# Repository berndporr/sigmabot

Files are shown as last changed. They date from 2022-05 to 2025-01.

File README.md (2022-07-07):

# sigmabot
Robot with linear servos and LIDAR

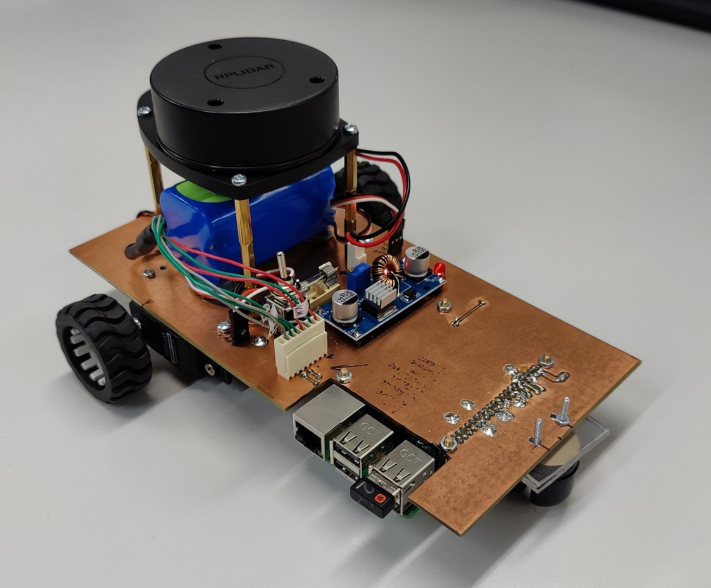
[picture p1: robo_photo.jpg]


## Power supply

TODO. Needs to be fixed.

## LiDAR

RPLIDAR A1M8 is a 360degree omnidirectional laser scanner, based on the
triangulation ranging technique that emits modulated laser signal in
the near-infrared (NIR) light band (typ. 785nm) and this signal is
then reflected by a detected object.

In this project the UART communication interface was used to transmit
LiDAR data to the RaspberryPi rather than the alternatively provided
USB, due to the comparative simplicity of the communication protocol
and the transmitted data packets, which in turn ensures a quicker data
transmission.  The LiDAR’s motor is powered directly from the battery
(7.4V), while the scanning systems is powered by regulated 5V volts,
in order to meet the manufacturer’s requirements.

## Continuous Rotation Servo Motors

To make the robot movable, two Parallax continuous-rotation(CR) servo
motors were used. CR servos are modified servos that offer
open-loop speed control instead of the usual servos’ closed-loop
position control. This modification turns them into DC motors with
integrated motor driver, which in turn enables the bidirectional
rotation. Both the rotation speed and direction of the servo shaft of
each motor is controlled by a pulse width modulated (PWM) signal. Yet,
the lack of motor encoder or speed sensor to provide speed feedback
makes the CR servos prone to differences between desired and actual
speeds. Both motors have been powered
by a 5V regulated signal generated by the buck converter. The control
signals of the motors are 50Hz PWM signals, generated by two
RaspberryPi GPIO pins, where the higher the PWM duty cycle, the higher
the supplied powered to the motors and the faster the motor rotation
would be.  When tested, the motors exhibited non-linear response of
speed to applied PWM duty cycle. Second-order polynomial equation has
been therefore derived to describe their relationship.

```
Speed = −0.0773(PWM)^2 + 0.1787(PWM) − 0.0075
```

where PWM duty cycle ∈ [0, 1] (with 1 corresponding to 100% duty
cycle, resulting in maximum speed).

## Mechanical Design

The idea of the mechanical design was to make something simple and
easily and cheaply manufacturable.  It was decided to use the main PCB
not only for electrical connections but also as the chassis of the
robot.  With that in mind the PCB was laid out while keeping to the
similar dimensions of the Alphabot.

There are only few other mechanical parts required. Namely the wheels,
the ball castor, and some custom 3D-printed fittings. The chosen
wheels were Pololu 1090 Wheels with dimensions of 42x19mm. In order to
fit these wheels onto the servo motor shafts a custom wheel adaptor
was 3D-printed.

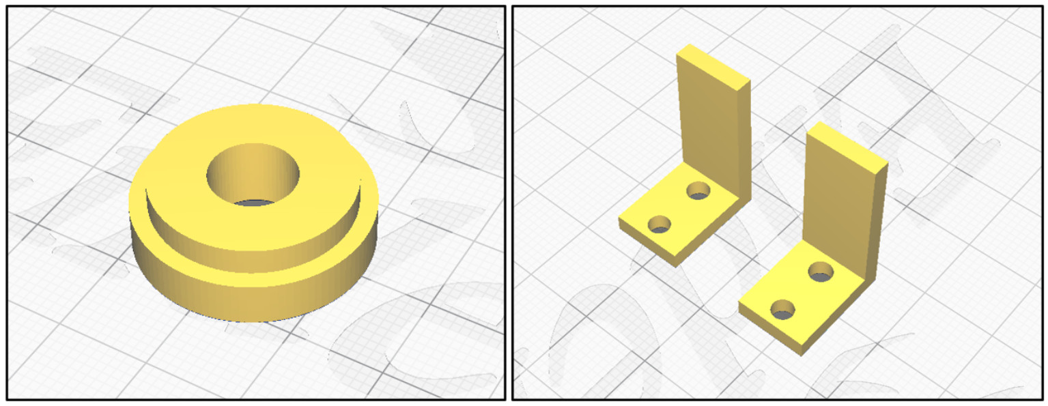
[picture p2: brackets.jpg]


# Further docs

https://github.com/berndporr/sigmabot/blob/main/doc.pdf

# Credits
 - Ilina Todorova <2326960T@student.gla.ac.uk>
 - Bernd Porr <bernd.porr@glasgow.ac.uk>

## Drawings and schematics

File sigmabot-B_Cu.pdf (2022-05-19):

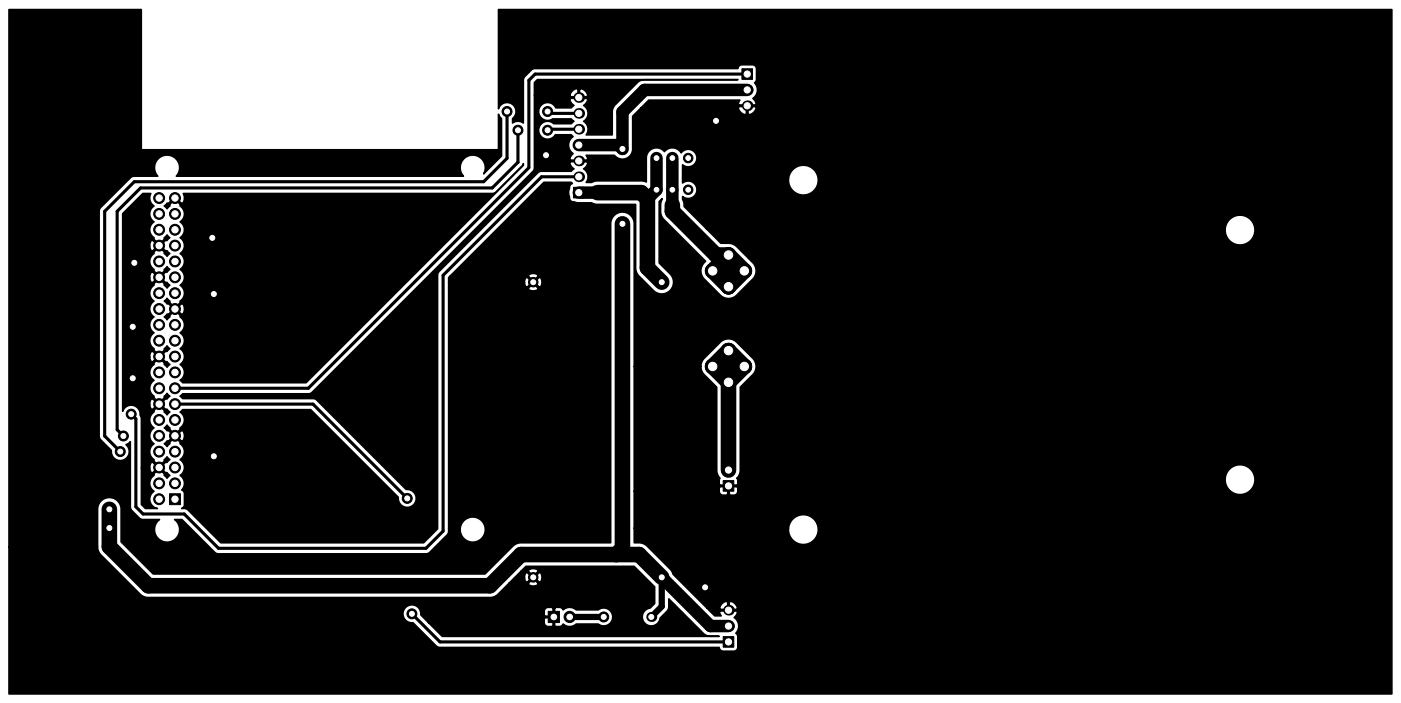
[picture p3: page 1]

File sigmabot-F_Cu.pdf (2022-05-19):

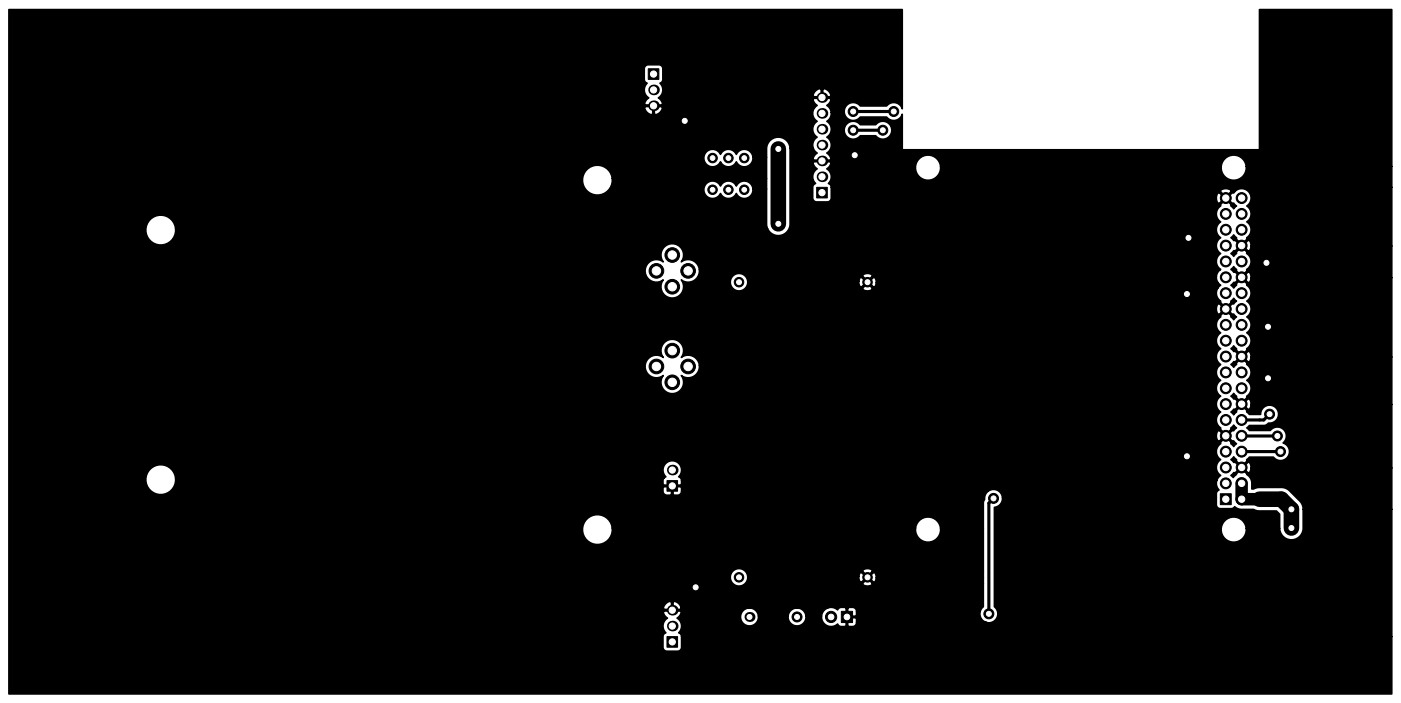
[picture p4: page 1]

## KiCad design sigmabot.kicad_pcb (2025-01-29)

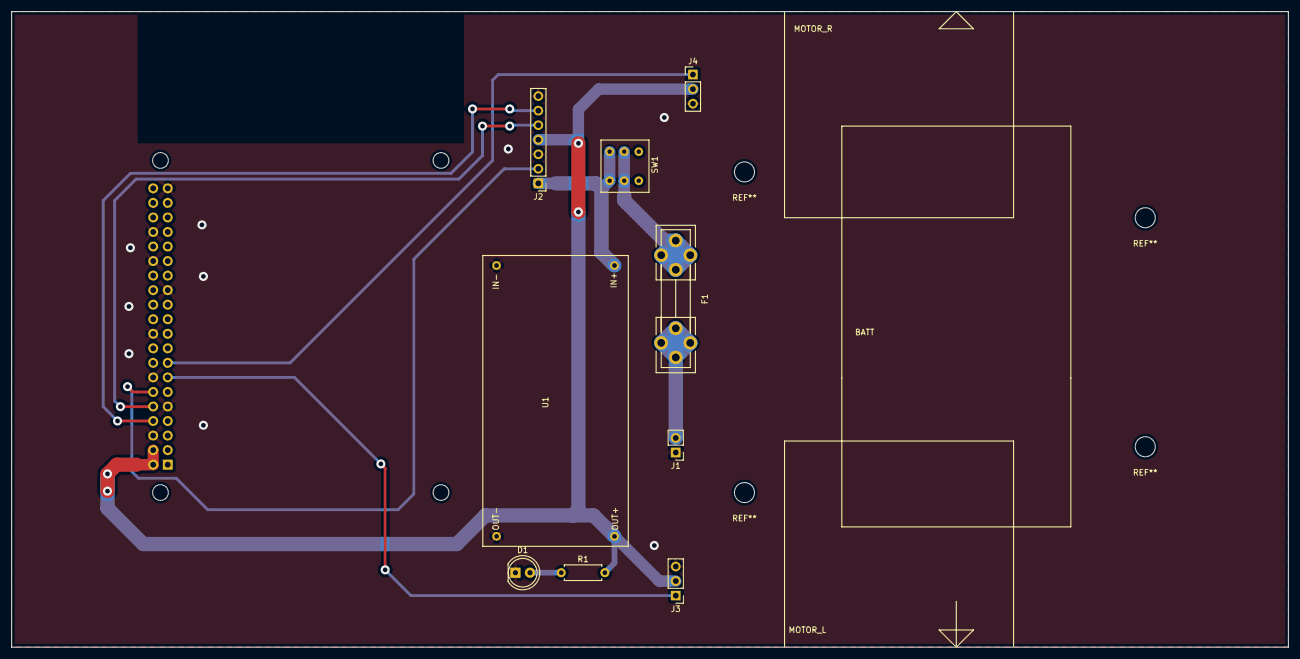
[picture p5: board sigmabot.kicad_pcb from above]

Board: 2 copper layers, 223.0 x 111.0 mm, 10 parts (0 on the bottom side), 11 nets.

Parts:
D1: LED; LED_D5.0mm
F1: Fuse; Fuseholder5x20_horiz_open_universal_Type-III
J1: Conn_01x02; PinHeader_1x02_P2.54mm_Vertical
J2: Conn_01x07; PinHeader_1x07_P2.54mm_Vertical
J3: MOTOR_L; PinHeader_1x03_P2.54mm_Vertical
J4: MOTOR_R; PinHeader_1x03_P2.54mm_Vertical
R1: 510R; R_Axial_DIN0207_L6.3mm_D2.5mm_P7.62mm_Horizontal
RP1: Raspberry_Pi_2_3; raspberrypi_2_3
SW1: SW_DPDT_x2; sw_DPDT
U1: BUCK_CONV

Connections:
+5V: J2.4, J3.2, J4.2, R1.2, RP1.2, RP1.4, U1.3
+BATT: J2.1, SW1.1, SW1.4, U1.1
GND: D1.1, J1.1, J2.3, J2.7, J3.3, J4.3, RP1.6, RP1.9, RP1.14, RP1.20, RP1.25, RP1.30, RP1.34, RP1.39, U1.2, U1.4
LIDAR_RX: J2.6, RP1.8
LIDAR_TX: J2.5, RP1.10
MOTO_CTRL: J2.2, RP1.12
unnamed: D1.2, R1.1
unnamed: F1.1, SW1.2, SW1.5
unnamed: F1.2, J1.2
PWM_L: J3.1, RP1.13
PWM_R: J4.1, RP1.15

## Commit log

2022-05-19 Added kicad files
    [sigmabot.kicad_pcb, sigmabot.sch]
2022-07-07 Removed power supply stuff as it's not working.
2025-01-29 Just opened and closed it in newest kicad and it updated the PCB.
    [sigmabot.kicad_pcb]
